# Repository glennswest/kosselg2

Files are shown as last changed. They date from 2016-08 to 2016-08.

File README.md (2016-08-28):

wolfstock
=========

__NOTE__ This is a Work In Progress

__NOTE__ The old T frame/Ostoc version of this has been deprecated and can be found in the branch [tframe](https://github.com/wolfmanjm/wolfstock/tree/tframe)

A 3d Delta printer based on the Mini-Kossel but using 2040 Makerslide for the
towers and the carriages, and accomodating larger bed and height.

* [Githubiverse page](http://wolfmanjm.github.com/wolfstock)
* [First Print](http://www.youtube.com/watch?v=khotvR7Lyf4)
* [Printing Tornado vase](http://www.youtube.com/watch?v=ChUlHnQ6QRw)
* [Printing](http://youtu.be/xLpwUxT9Mxs)
* [Swirling Urn print](http://flic.kr/p/fC9EcJ)

This is a Makerslide and Misumi based frame, using Spectra fishing
line drive ala original Kossel, or gt2 belts with crown pulleys.

It has a large frame made from 2040 and 2020 Misumi extrusion using
mini-kossel style printed brackets.

The default version has 1000mm high Makerslide towers, an 463.4mm triangle
sides, and arm length of 370mm, which makes for a roughly 250mm circular build
area using Traxxas joints and 400mm build height. Use the Kossel Calculator
and the lite-frame.scad to play with the exact lengths required. If you were
to use mag arms which have more degrees of movement the build area would be
around 350mm diameter for the above dimensions.

The drive system can use Spectra 60lb braided fishing line and machined spools
and 608 bearings for the idlers.

There is an alternate set of stls that make use of gt2 belt. In this case the
preferred idler is composed of two back to back 695 flanged bearings and the
`tensioner-gt2-F695zz.stl` file, but there is also a `crownedpulley.stl` that fits
over a 608 bearing and the file `tensioner_g2_608.stl` will house that. I have
found that the crowned pulleys do not seem to keep the belt aligned as they
are supposed to.

Most scad source files are parameterized so the dimensions can be
tweaked.

Some of the scad files are derived from Kossel files or other scad files, most
are original designs. The original source of the file is usually cited in the
code.

This work is licensed under the Creative Commons
Attribution-ShareAlike 3.0 Unported License. To view a copy of this
license, [visit](http://creativecommons.org/licenses/by-sa/3.0/)

## BoM

### Printed parts
Stls are in the
[STL directory](https://github.com/wolfmanjm/wolfstock/tree/master/stl)

* Print three `base-bracket-motor.stl`
* Print three `base-bracket-idler.stl`
* Print three `tensioner_608.stl` *OR* `tensioner_g2_608.stl` (also the `crownedpulley.stl` if using the latter) *OR* three `tensioner-gt2-F695zz.stl`
* Print one `effector.stl`
* Print three `carriage-new.stl` *OR* `gt2-carriage.stl` These bolt onto a carriage that has
  20mm hole paterns
  [like this](https://www.inventables.com/technologies/standard-wheel-carriage-plate),
  so check your plates and adjust the scad as necessary.
* Effector mounted extruder from http://www.thingiverse.com/thing:42112 with pg35l Stepper from http://www.ultibots.com/ (I use some aluminum stadoffs to raise the extruder about an inch.

### Extrusion and Vitamins
* 3x 1m lengths of 2040 Makerslide, OR 3x 1m lengths of Misumi 2040 and
  3x 1m lengths of open rail, OR 3x 1m lengths of 2040 V-Slot
* 3x 463.4mm lengths of 2040 for bottom rails (use the kossel
  calculator to get the length you want and add in the side offset,
  see the lite-frame.scad and play with the sizes)
* 3x 463.4mm lengths of 2020 for top rails
* 12x delrin v wheels for whatever rails you have chosen (sourcing
  below)
* Appropriate carriage for the rails and wheels, add 2x eccentric
  spacers per carriage and 3x regular spacers. (some wheels come with
  the regular ones)
* 6x 370mm 0.318" (8mm) square carbon fiber tube if using the endcaps to join
  with traxas joints, or round tubing as per Kossel like these from
  [Goodwinds](http://goodwinds.com/20015.html), where the traxxas joints may slip in with some hot glue
* plenty of t nuts and M5 bolts...
  lengths M5x16 for the back 18 total, M5x12 for the sides 32 total

## Sourcing

### Common components

* Bottom side rails [Misumi][] HFS5-2040-500 $5.40 3 $16.20
* Top side rails  [Misumi][] HFS5-2020-500 $2.85 3 $8.55
* Bolts for back of towers M5 Length 16mm
* Bolts for side braces M5 Length 12mm
* T Nuts M4 100 pack  [Misumi][] HNKK5-5 $20

### Drive Mechanism

Choose one of the following...

#### Fishing Line
* Spectra 60lb braided fishing line
* [Drive spools](http://3d.grabercars.com/?product=filament-drive-reel-grooved-delrin-18mm-o-d-for-kossel) $7.95 3 $23.85
* 3x 608 bearings for idler, and use tensioner_608.stl

#### GT2 Belt
* [GT2 Belt](http://www.robotdigg.com/product/10/Open-Ended-6mm-Width-GT2-Belt) $2.00/meter approx 6.3-7 meters $14.00
* [GT2 toothed pulley 20 Teeth 5mm Bore](http://www.robotdigg.com/product/9/GT2-Pulley-20-Teeth-5mm-Bore) $2.00 3 $6.00
* 3x 608 bearings and use `tensioner_g2_608.stl` idler and `crownedpulley.stl` OR
  6x F695zz flanged bearings and use `tensioner-gt2-F695zz.stl`, the latter seems to work better, and are
  [available here](http://www.ebay.com/itm/180915657724) 10 for $9.67 free shipping
* [Grub screws for pulley](http://www.robotdigg.com/product/17/M3*4-Grub-Screw-PACK-SET-for-Timing-Pulleys) $0.35

### Makerslide based
* [Makerslide rail 1000mm](https://www.inventables.com/technologies/makerslide) 25142-03 $21.74 3 $65.52
* [Dual Bearing V-Wheel Kit](https://www.inventables.com/technologies/dual-bearing-v-wheel-kit) 25203-02 $4.85 12 $58.20
* [Eccentric Spacer](https://www.inventables.com/technologies/eccentric-spacer) 25195-01 $2.00 6 $12.00
* [Nylon Spacer pack of 10](https://www.inventables.com/technologies/nylon-natural-color-spacer) 25206-01 $2.00 1 $2.00
* [Standard Wheel Carriage Plate](https://www.inventables.com/technologies/standard-wheel-carriage-plate) 25200-01 $8.00 3 $24.00

Sub Total: $161.72

### V Slot based
* [V-Slot 20 x 40mm 1000mm](http://openbuildspartstore.com/v-slot-20-x-40mm/) $13.00 3 $39.00
* [OpenBuilds Dual V Wheel Kit - Delrin](http://openbuildspartstore.com/openbuilds-dual-v-wheel-kit-delrin/) $3.85 12 $46.20
* [V-Slot Universal Plate](http://openbuildspartstore.com/v-slot-universal-plate) $12.00 3 $36.00
* [Eccentric Spacers](http://openbuildspartstore.com/eccentric-spacers/) $2.00 6 $12.00

Sub Total: $133.20

### Open Rail Based
* 2040 1000mm  [Misumi][] HFS5-2040-1000 $10.80 3 $32.40
* [Open Rail 1000mm](http://openbuildspartstore.com/openrail-black-anodized/) $6 6 $36
* [OpenBuilds Dual V Wheel Kit - Delrin](http://openbuildspartstore.com/openbuilds-dual-v-wheel-kit-delrin/) $3.85 12 $46.20
* [OpenRail Gantry Plate 40mm](http://openbuildspartstore.com/openrail-gantry-plate-universal-mount) $8.00 3 $24.00
* [Eccentric Spacers](http://openbuildspartstore.com/eccentric-spacers/) $2.00 6 $12.00

Sub Total: $150.60

### Printed carriage for Makerslide or Open Rail
For the cheapeast solution print `carriage-plate.stl` and just buy the v wheels.
This saves having to get the expensive aluminum plates and eccentric spacers.
That saves $36 on the open rail version and a lt more on the makerslide version.

* [OpenBuilds Dual V Wheel Kit - Delrin](http://openbuildspartstore.com/openbuilds-dual-v-wheel-kit-delrin/) $3.85 12 $46.20

### Notes
You can use the printed carriage for each tower, saving about $36 or more

## Assembly

1. Bolt the side rails in first to form the triangle. Remember to put
enough tslot nuts in the tslots first, also put some in the top and
side for mounting things later.
2. Mount the motors next.
3. Insert the Makerslide into the holes, use a rubber mallet to get the corners on the makerslide, but be gentle.
4. bolt the makerslide from the back.
5. do the same for the top, but remember to put the idlers in the track first

# License

<br /><span xmlns:dct="http://purl.org/dc/terms/" property="dct:title">Wolfstock</span> by <a xmlns:cc="http://creativecommons.org/ns#" href="http://wolfmanjm.github.com/wolfstock" property="cc:attributionName" rel="cc:attributionURL">Jim Morris</a> is licensed under a <a rel="license" href="http://creativecommons.org/licenses/by-sa/3.0/deed.en_US">Creative Commons Attribution-ShareAlike 3.0 Unported License</a>.<br />Based on a work at <a xmlns:dct="http://purl.org/dc/terms/" href="https://github.com/wolfmanjm/wolfstock" rel="dct:source">https://github.com/wolfmanjm/wolfstock</a>.

[Misumi]: http://www.misumi-ec.com "Misumi"

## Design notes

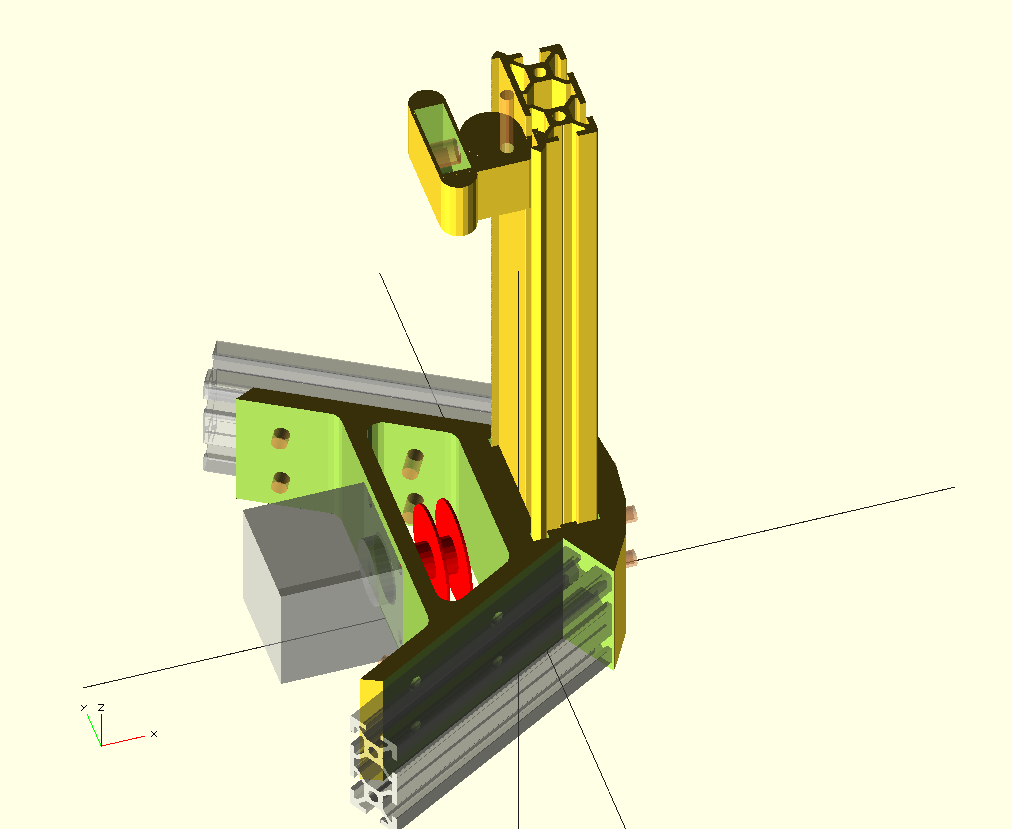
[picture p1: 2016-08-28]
img/belt-idler.png

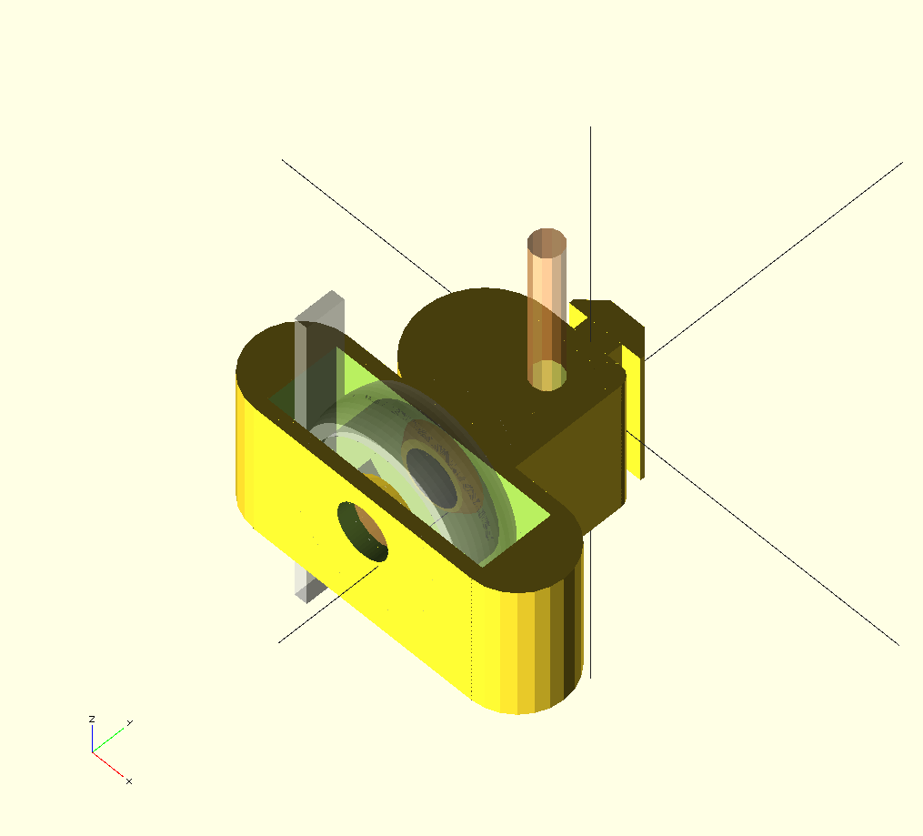
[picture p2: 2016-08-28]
img/g2-belt-idler.png

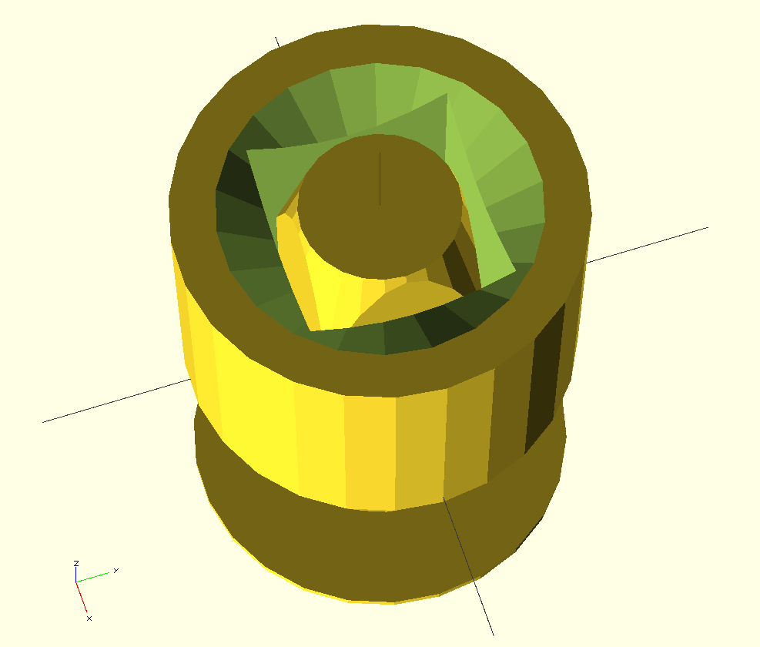
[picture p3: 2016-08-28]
img/rod-end.png

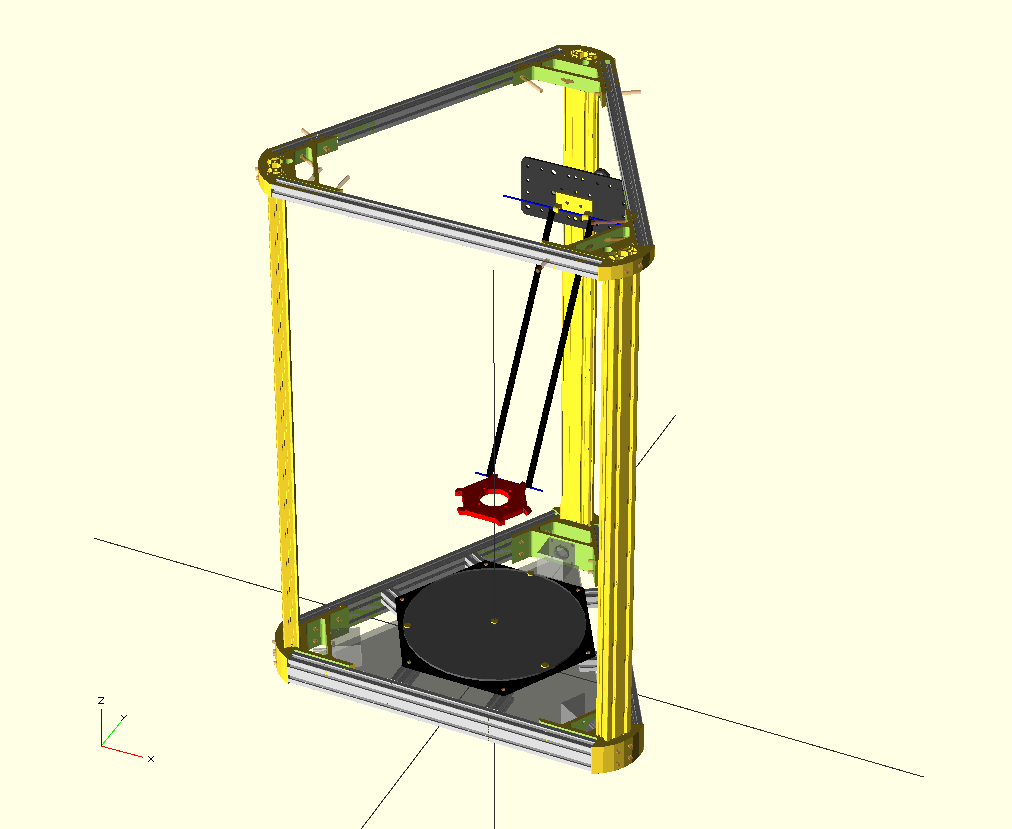
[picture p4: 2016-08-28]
img/lite-frame.png

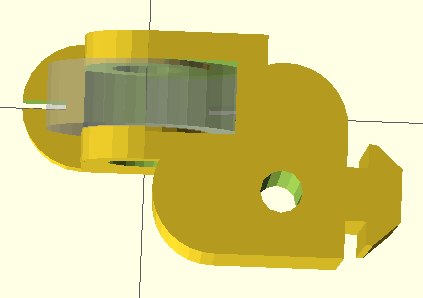
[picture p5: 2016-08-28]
img/tensioner-top.png

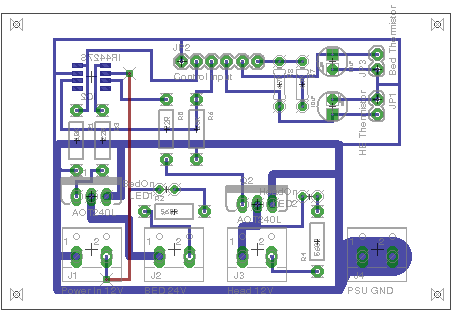
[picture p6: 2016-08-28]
circuits/mosfetpcb.png

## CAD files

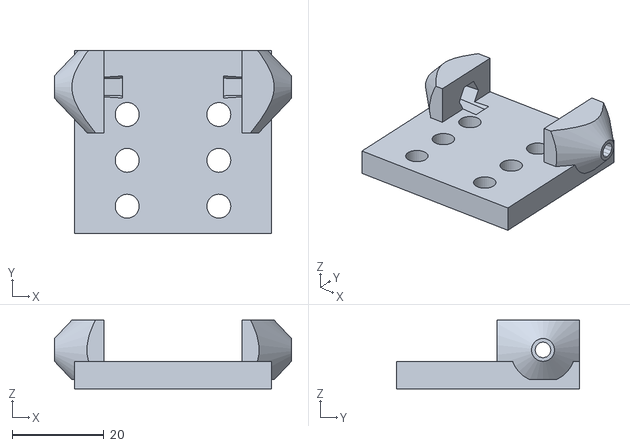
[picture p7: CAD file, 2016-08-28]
carriage-new.stl
51.7 x 40.0 x 15.0

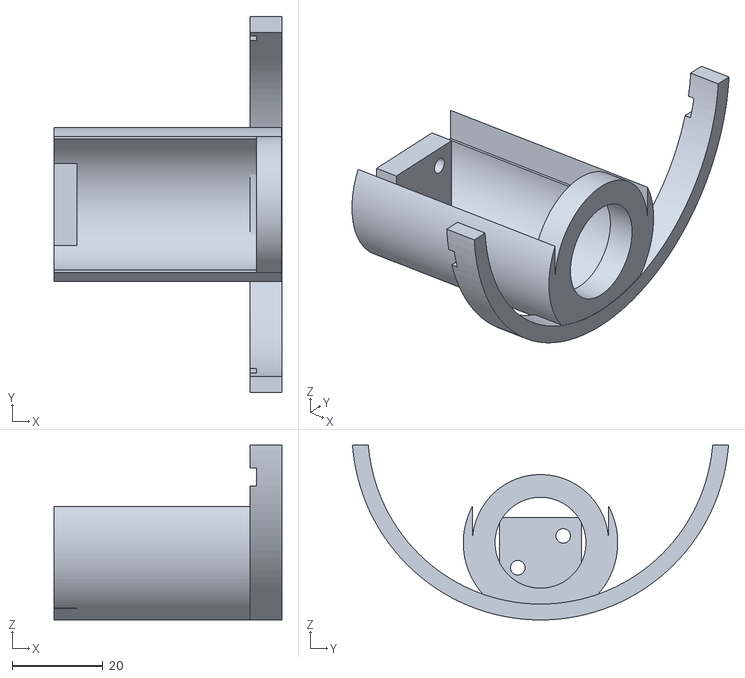
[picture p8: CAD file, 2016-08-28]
fixmount/sensormount.stl
50.1 x 82.8 x 38.5

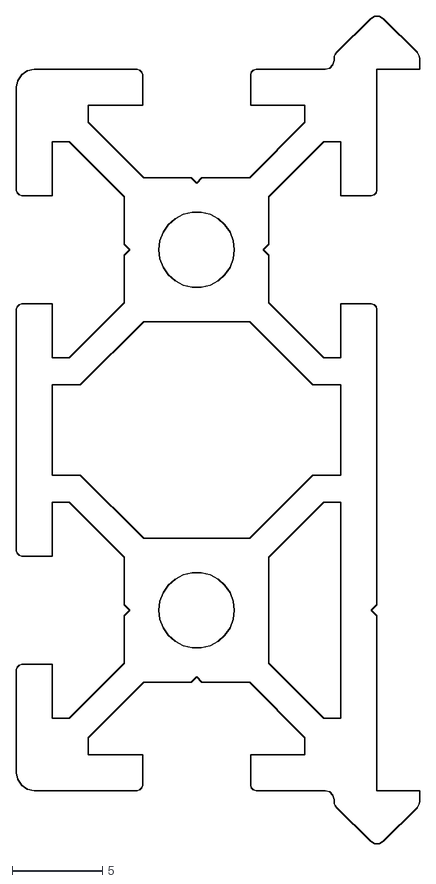
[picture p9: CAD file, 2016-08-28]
makerslide/makerslide_extrusion_profile.dxf
22.4 x 45.9

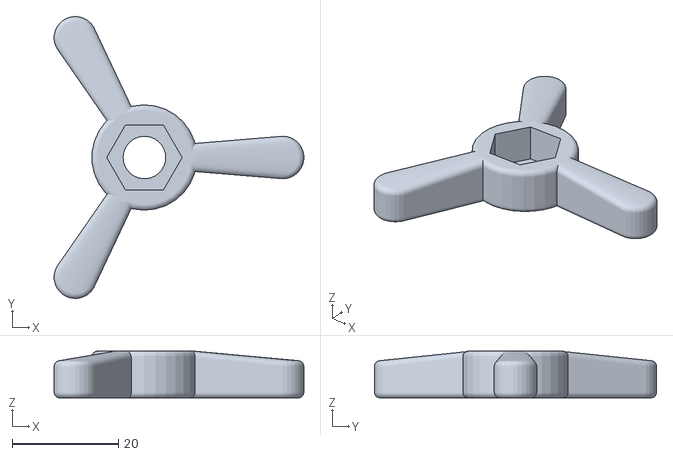
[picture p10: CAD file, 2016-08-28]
stl/thumbnut.stl
47.0 x 53.0 x 8.79

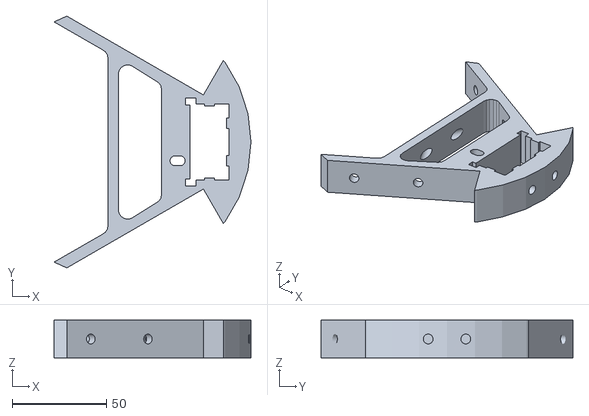
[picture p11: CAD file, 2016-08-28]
base-bracket-idler.stl
104.7 x 133.8 x 20.0

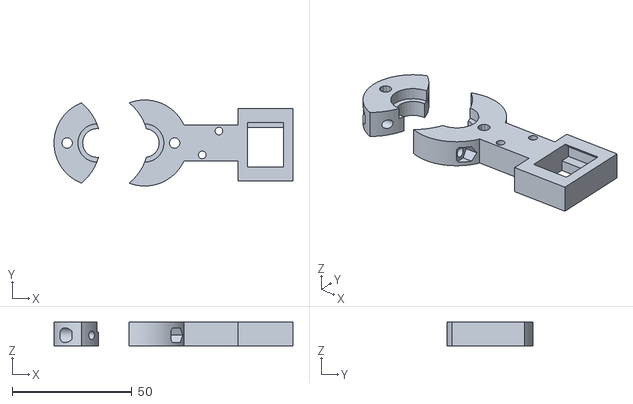
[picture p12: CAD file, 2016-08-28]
fixmount/e3dmountring.stl
100.0 x 36.0 x 10.0

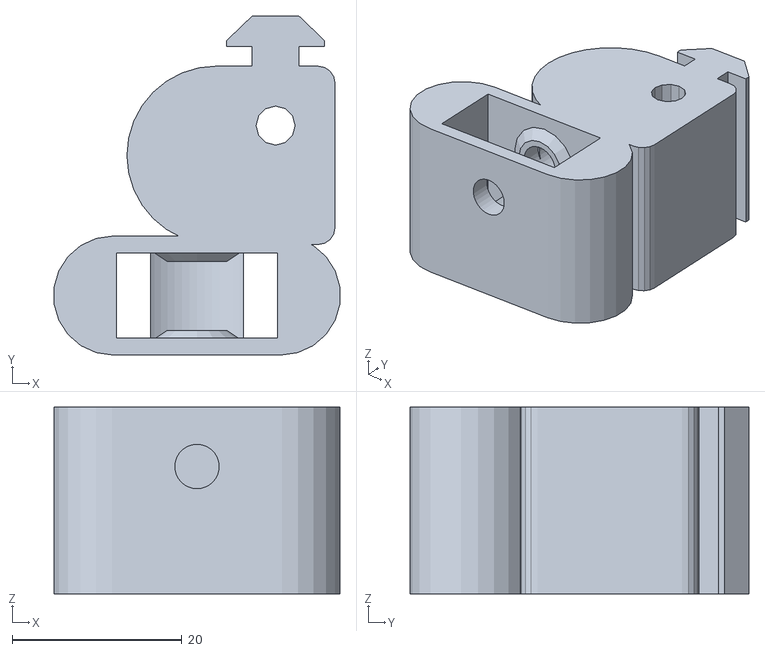
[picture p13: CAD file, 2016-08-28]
stl/tensioner-gt2-F695zz.stl
33.7 x 39.9 x 22.0

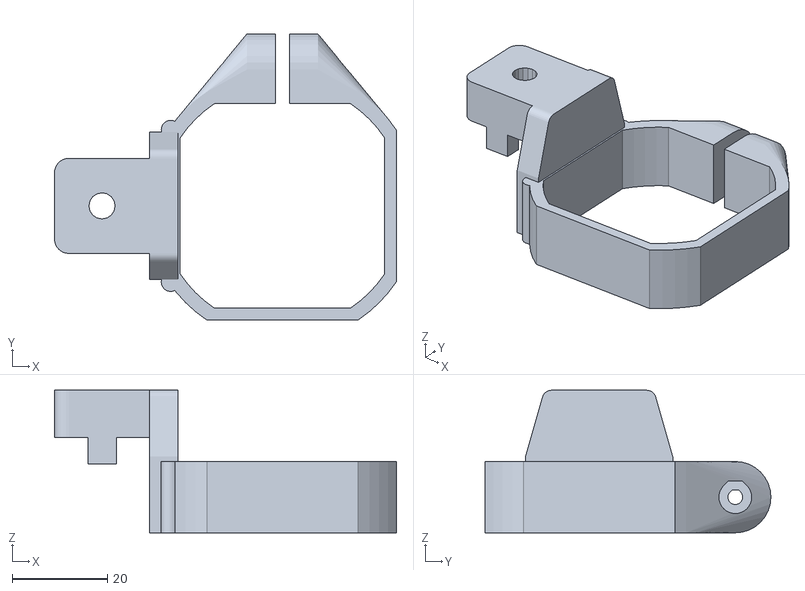
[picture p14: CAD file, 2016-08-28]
fixmount/nema17stepper-mount_v2.stl
72.0 x 60.1 x 30.0

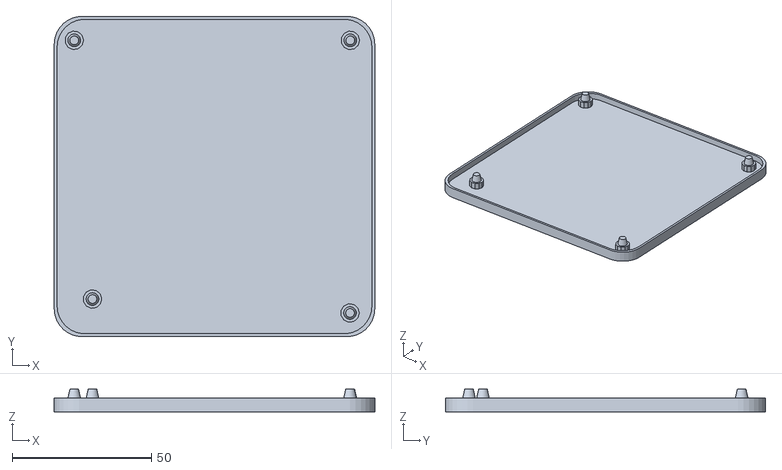
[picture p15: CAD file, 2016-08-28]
smoothie-box.stl
115.1 x 114.9 x 8.20

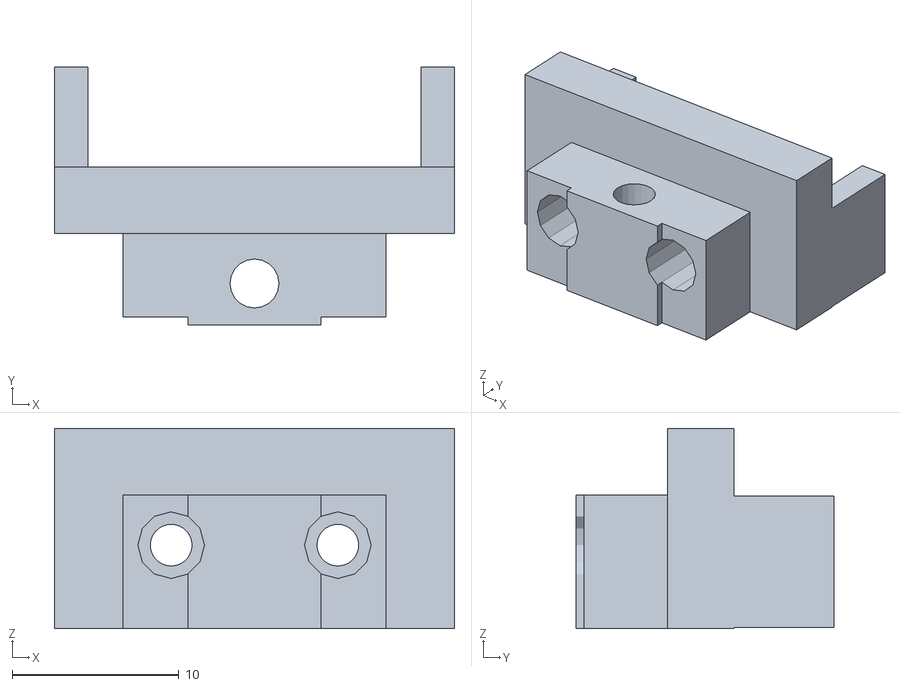
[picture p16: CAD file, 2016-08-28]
stl/adjustable-limit-stop-slide.stl
24.0 x 15.5 x 12.0

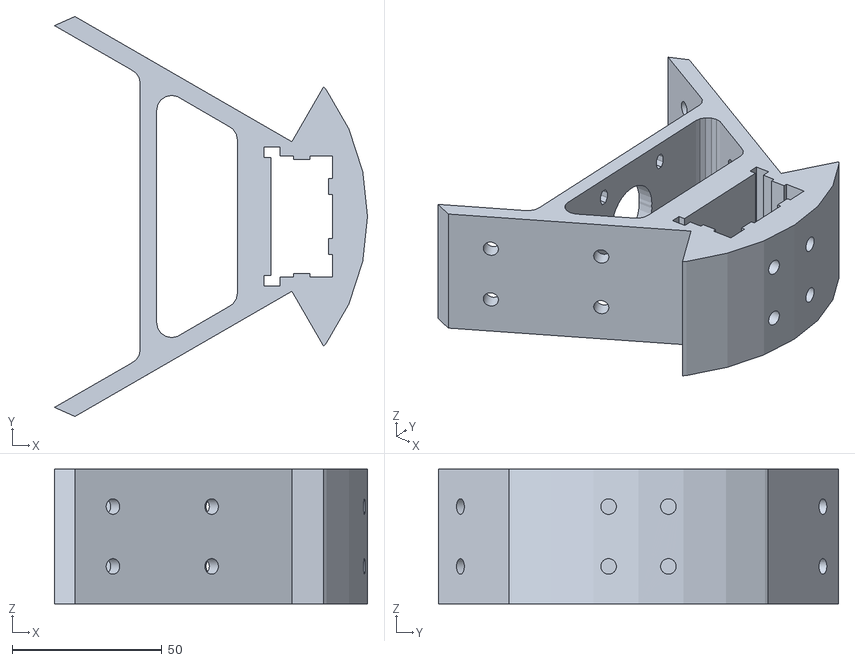
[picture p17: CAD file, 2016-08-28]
base-bracket-motor.stl
104.7 x 133.8 x 45.0

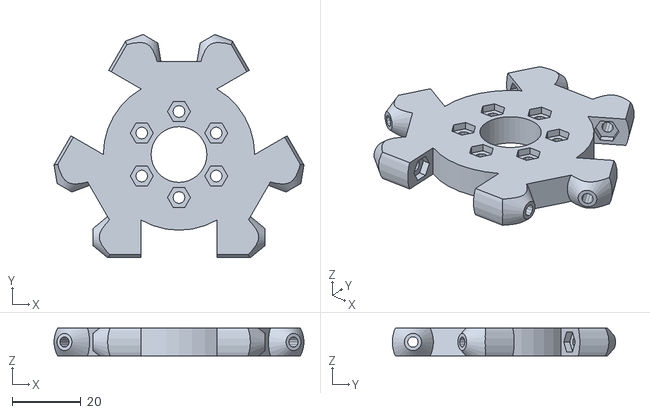
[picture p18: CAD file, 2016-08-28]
fixmount/effector50.stl
72.7 x 64.8 x 8.00

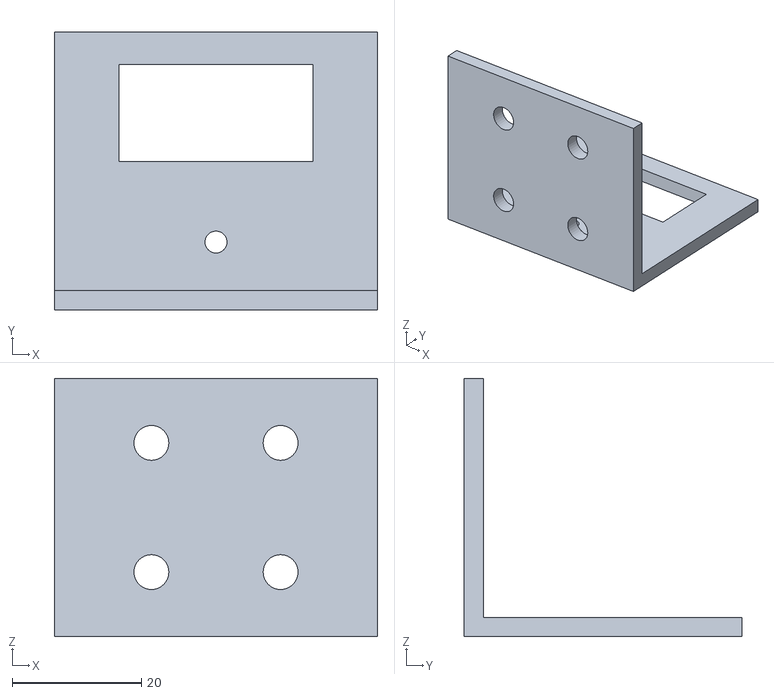
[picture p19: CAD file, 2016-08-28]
stl/eswitch-holder.stl
50.0 x 43.0 x 40.0

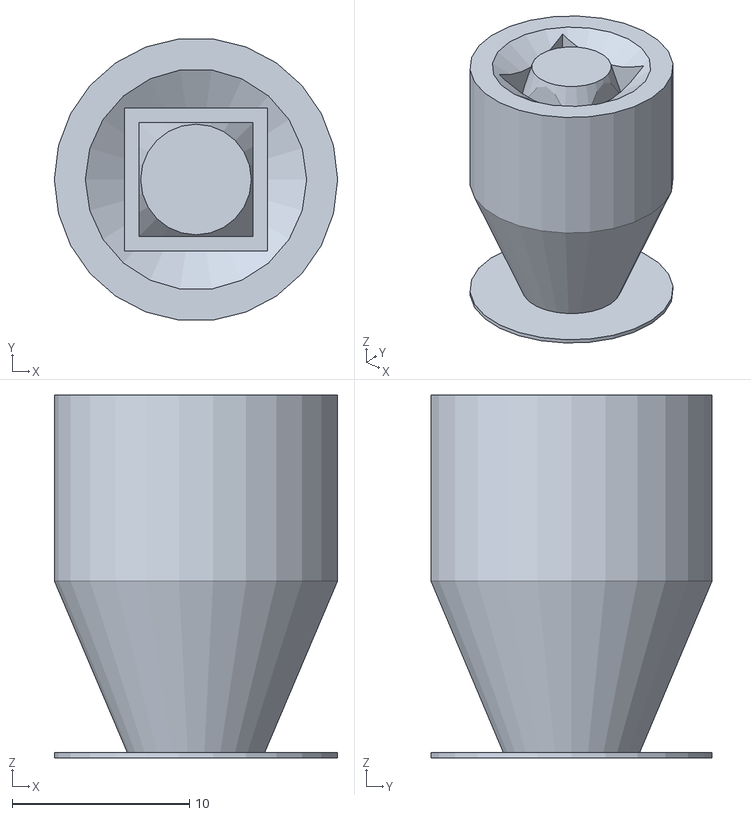
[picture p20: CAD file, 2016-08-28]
stl/rod-end-connector.stl
16.0 x 15.9 x 20.5

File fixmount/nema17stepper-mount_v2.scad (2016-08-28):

//remix of http://www.thingiverse.com/thing:528934
//
//-- NEMA 17 stepper holder for 2020 rail
//  designed by L Buell  Feb 2016
//-- remixed from a well designed remix by AndrewBCN - November 2014
//-- remixed from an original (excellent) design by Paul Chase
//-- original design is Thingiverse no. 321523

//  I removed some of AndrewBCN's stuff and added the 2020 mount
// some of my 2020 rail mounted designs are meant to be drop onto the rail,
//   and some are meant to more fully engage and slide in from the end of the rail
// this design is drop-in style

//-- slop is tolerance, wall is wall thickness
slop = 0.2; // don't mess with these two!
wall = 3;

base_plate_height = 16;
Vert_plate_thickness = 6; // vertical base plate thickness
motor_w = 42;
motor_r = 50/2;
$fn=32;
height = wall+12;
m5 = 5.5;           // threaded z-rod diameter
m3 = 3.3/2;     // diam of m3 screw
m3n = 6.9/2;  // diam of m3 nut
m3nh = 4;      // nut height of m3 nuts that hold adaptor to x-ends
m3nl = 20;     // screw length of nuts that hold adaptor to x-ends
hole_sep = 20;  // separation of mount holes - mount holes deleted - this now controls height of mount

rail_Ht=20;  //height of 2020 rail 
2020_mount_width=20;  // width of mounting arm on top of 2020 rail
2020_mount_thickness=10;  // thickness of mounting arm on top of 2020 rail
mount_radius=3;  //radius of corners of rounded block
2020_groove_size=6; //used for the width and depth of the block fitting into the 2020 rail
Tslot_nut_length=12;  //length of T-slot nut

complete_part();
//mirror(0,0,1) complete_part();

module complete_part(){
difference(){
union(){
stepper_holder();	
translate([-motor_w/2-2020_mount_width/2-Vert_plate_thickness-.95,0,10+hole_sep-2020_mount_thickness/2])2020_block();  //block that mounts into the 2020 rail
}  //union
// cavities

// 2020 mounting block cavities
translate([-motor_w/2-2020_mount_width/2-Vert_plate_thickness-.95,-2020_mount_width/2,0]){
//cutout for t-slot nut
translate([-2020_mount_width/2+rail_Ht/2-2020_groove_size/2-.5,(2020_mount_width-Tslot_nut_length)/2,rail_Ht-2020_groove_size-.5])cube([2020_groove_size+1,Tslot_nut_length,2020_groove_size+.5]);
// hole for t-slot nut
translate([-2020_mount_width/2+rail_Ht/2,2020_mount_width/2,rail_Ht+2020_mount_thickness/2])cylinder(h=rail_Ht, r=5.5/2,center=true,$fn=16);
}  // translate
}  //difference
}  //module

module 2020_block(){
rounded_rectangle([rail_Ht,2020_mount_width,2020_mount_thickness],mount_radius,center=true);
// fill in rounded corner
translate([rail_Ht/2-3,-2020_mount_width/2,-2020_mount_thickness/2])cube([Vert_plate_thickness,2020_mount_width,2020_mount_thickness]);
// square block to fit in slot on rail
translate([-2020_groove_size/2,-2020_mount_width/2,-2020_mount_thickness/2-2020_groove_size+.5])cube([2020_groove_size,2020_mount_width,2020_groove_size]);
}  //module 2020_block

module stepper_holder() {
	scale_slop = 1.025; // another tolerance
	scale_size = (motor_w+wall+wall)/motor_w;	
	difference(){
		union(){
			hull(){
				//strap
				scale([scale_size,scale_size,1]) motor_base(h=height);
				//clamp
				translate([0,motor_w/2+wall+m3+wall,height/2]) rotate([0,90,0]) cylinder(r=height/2, h=5*wall, center=true);			
			}
			//mount base
			hull(){
				// bottom block of mount
				translate([-motor_w/2-wall-wall/2+0.55,0,base_plate_height/2]) cube([Vert_plate_thickness,31,base_plate_height], center=true);
				//  top cylinders that make top of mount
				translate([-motor_w/2-wall-wall/2+0.55-Vert_plate_thickness/2,+10,8+hole_sep]) rotate([0,90,0]) cylinder(r=2, h=Vert_plate_thickness);
				translate([-motor_w/2-wall-wall/2+0.55-Vert_plate_thickness/2,-10,8+hole_sep]) rotate([0,90,0]) cylinder(r=2, h=Vert_plate_thickness);				
			}
			// reinforcement cylinders in corners
			translate([-motor_w/2-wall-wall+3.5,+16,0]) rotate([0,0,0]) cylinder(r=2, h=15);
			translate([-motor_w/2-wall-wall+3.5,-16,0]) rotate([0,0,0]) cylinder(r=2, h=15);
		}  //union

		//cavities
		// slit
		translate([0,motor_w/2,height/2]) cube([wall,motor_w,height+1],center=true);
		// clamp holes
		render() translate([0,motor_w/2+wall+m3+wall,height/2]) rotate([0,90,0]) clamp_holes();
		// motor cross section hollowed out
		scale([scale_slop,scale_slop,1]) translate([0,0,-.05]) motor_base(h=height+.1);
	}
	
	// uncomment this if you need a place to tie wires to
	/*
	//-- AndrewBCN: I added a place where people can tie some wires
	difference(){
	   rotate([0,0,-90]) translate([22.5,+8,0]) cube([8,8,4]);
	   rotate([0,0,-90]) translate([26.5,+10,-2]) cube([1.5,4,12]);
	}
	*/	
} //module stepper_holder

module clamp_holes() {
	len = wall*5;
	// screwhole
	rotate([0,0,-90]) cap_cylinder(r=3.1/2, h=len*2, center=true); 
	// nut is on the inside
	mirror([0,0,1]) translate([0,0,wall*2.5]) rotate([0,0,-90]) cylinder(r=6.9/2, h=len, $fn=6);
	// screw is on the outside
	translate([0,0,wall*2.5]) rotate([0,0,-90]) cap_cylinder(r=6.9/2, h=len);
}

module cap_cylinder(r=1, h=1, center=false){
	render() union() {
		cylinder(r=r, h=h, center=center);
		intersection(){
			rotate([0,0,22.5]) cylinder(r=r/cos(180/8), h=h, $fn=8, center=center);
			translate([0,-r/cos(180/4),0]) rotate([0,0,0]) cylinder(r=r/cos(180/4), h=h, $fn=4, center=center);
		}
	}
}

//-- Motor cross section
module motor_base(h=wall){
	intersection(){
		translate([0,0,h/2]) cube([motor_w, motor_w, h], center=true);
		cylinder(r=motor_r+slop, h=h, $fn=64);
	}
}

// From: https://github.com/T3P3/Mendel90/tree/LaserCut/scad
// utils.scad
module rounded_square(w, h, r){
    union() {
        square([w - 2 * r, h], center = true);
        square([w, h - 2 * r], center = true);
        for(x = [-w/2 + r, w/2 - r])
            for(y = [-h/2 + r, h/2 - r])
                translate([x, y])
                    circle(r = r);
    }
}
// From: https://github.com/T3P3/Mendel90/tree/LaserCut/scad
// utils.scad
module rounded_rectangle(size, r, center = true){
    w = size[0];
    h = size[1];
    linear_extrude(height = size[2], center = center)
        rounded_square(size[0], size[1], r);
}

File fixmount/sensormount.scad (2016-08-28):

// main module
rotate([0,90,0])main();

$fn=128;

module main() {
  
  difference(){
      translate([ -4,-9,-4.5]) cube([20,18,5]);
      translate([  7,-5,-5.5]) cylinder(r=1.6,h=12);
      translate([  0,+5,-5.5]) cylinder(r=1.6,h=12);
      }
   
   difference(){
       union(){
         translate([11,-7.5,-4.5]) cube([5,15,50]);  
         translate([1.5,0,-4.5]) cylinder(r=17,h=50);
       }
       translate([1.5,0,-5.5]) cylinder(r=14.5,h=53);
       translate([-30,-15,-5.5]) cube([30,30,52]);
       }
      difference(){ 
        translate([1.5,0, 40]) cylinder(r=15,h=5.5);  //9.5
        translate([1.5,0, 39.2]) cylinder(r=10,h=6.4);
        }
      difference(){  
        translate([-23.0,0,38.6]) cylinder(r=41.5,h=7);
        translate([-23.0,0,36.6]) cylinder(r=38,h=10);
        translate([ -104,-42,38]) cube([84,84,12]);
        translate([ -15,-42,28]) cube([4,84,12]);  
        }  
      
  }

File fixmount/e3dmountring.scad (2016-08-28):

// J-Head (E3D) mount
// copyright (c) 2013 - Jarek Szczepanski <imrahil@imrahil.com>
// oryginal design derived from http://www.thingiverse.com/thing:26355

use <keystone.scad>

$fn=256;

size = 18;
length = 28;
height = 9;

separation = 50;  // Distance between ball joint mounting faces.
offset = 20;  // Same as DELTA_EFFECTOR_OFFSET in Marlin.
mount_radius = 12.5;  // Hotend mounting screws, standard would be 25mm.
hotend_radius = 8.1;  // Hole for the hotend (J-Head diameter is 16mm).
push_fit_height = 4;  // Length of brass threaded into printed plastic.
height = 10;
cone_r1 = 2.5;
cone_r2 = 14;


mount_spacing = 50;
carriage_mount_dia = 4.5;

// dimensions for E3D hotned
extruder_dia = 16;
extruder_dia2 = 12;
extruder_cyl1_height = 3.7;
extruder_cyl2_height = 5.6;

mount_screws_dia = 3.5;

// Increase this if your slicer or printer make holes too tight.
extra_radius = 0.1;

// OD = outside diameter, corner to corner.
m3_nut_od = 6.1;
m3_nut_radius = m3_nut_od/2 + 0.2 + extra_radius;

// Major diameter of metric 3mm thread.
m3_major = 2.85;
m3_radius = m3_major/2 + extra_radius;
m3_wide_radius = m3_major/2 + extra_radius + 0.2;


// main module
main();

module main() {
  translate([62,-16,-4.5]) rotate([0,0,90]) keystone();
  difference(){
      translate([16,-7.5,-4.5]) cube([23,15,height]);
      translate([31,+5,-5.5]) cylinder(r=1.6,h=12);
      translate([24,-5,-5.5]) cylinder(r=1.6,h=12);
      }
  translate([-20, 0, 0]){
    intersection() {
      mount();
      separator();
    }
  }

  difference() {
    mount();
    separator();
  }
}

module mount() {
  difference() {
    plate();
    extruder();
    mount_screws();
  }
}

module plate() {
  difference() {
  
       translate([0,0,-4.5]) cylinder(r=18, h=height);
   
   
  for (a = [90:180:359]) rotate([0, 0, a]) {
      translate([0, mount_radius, 0])
	cylinder(r=m3_wide_radius+.5, h=2*height, center=true, $fn=12); // Add /5 to give us room for brass
    //  translate([0, mount_radius, height-4.4]) 
    //    cylinder(r=m3_nut_radius, h=3, center=true, $fn=6);
    }  
  }
}

module extruder() {
  pos1 = height/2 - extruder_cyl1_height/2 + 0.5;
  pos2 = height/2 - extruder_cyl1_height - extruder_cyl2_height/2;

  union() {
    translate([0, 0, pos1]){
      cylinder(r=extruder_dia/2, h=extruder_cyl1_height + 1, center=true, $fn=32); 
    }

    translate([0, 0, pos2]){
       cylinder(r=extruder_dia2/2, h=extruder_cyl2_height + 1, center=true, $fn=32); 
    }	
  }
}

module mount_screws() {
  union() {
    translate([0, 12, 0]){
      rotate([0, 90, 0]) cylinder(r=mount_screws_dia/2, h=length + 3, center=true, $fn=32); // hole for nut
      translate([length/2 - 3, 0, 0]){
        rotate([-90, 0, -90]) cylinder(r=mount_screws_dia, h=5, $fn=6); 
      }
      translate([-length/2 - 1.5, 0, 0]){
        rotate([0, 90, 0]) cylinder(r=3.1, h=5, $fn=32); // hole for screw's head
      }
    }

    translate([0, -12, 0]){
      rotate([0, 90, 0]) cylinder(r=mount_screws_dia/2, h=length + 3, center=true, $fn=32); // hole for nut 
      translate([length/2 - 3, 0, 0]){
        rotate([-90, 0, -90]) cylinder(r=mount_screws_dia, h=5, $fn=6); 
      }
      translate([-length/2 - 1.5, 0, 0]){
        rotate([0, 90, 0]) cylinder(r=3.1, h=5, $fn=32); // hole for screw's head 
      }
    }
  }
}

module separator() {
  translate([-20, 0, 0]){
    cylinder(r=43/2, h=height + 1, center=true, $fn=64); 
  }
}

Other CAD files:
stl/adjustable-limit-stop.stl
stl/adjustable-limit-stop-mount.stl
stl/carriage-plate.stl
stl/2020-insert.stl
configuration.scad
2020-insert.scad
MCAD/bearing.scad
MCAD/bitmap/alphabet_block.scad
MCAD/bitmap/bitmap.scad
MCAD/bitmap/height_map.scad
MCAD/bitmap/letter_necklace.scad
MCAD/bitmap/name_tag.scad
MCAD/boxes.scad
MCAD/constants.scad
MCAD/curves.scad
MCAD/gears.scad
MCAD/gridbeam.scad
MCAD/hardware.scad
MCAD/involute_gears.scad
MCAD/materials.scad
MCAD/math.scad
MCAD/metric_fastners.scad
MCAD/motors.scad
MCAD/nuts_and_bolts.scad
MCAD/regular_shapes.scad
MCAD/screw.scad
MCAD/servos.scad
MCAD/shapes.scad
MCAD/stepper.scad
MCAD/teardrop.scad
MCAD/triangles.scad
MCAD/units.scad
MCAD/utilities.scad
Orbitron_Medium.scad
arm-mount.scad
arm-plate.scad
base-bracket-idler.scad
base-bracket-motor.scad
card.scad
carriage-new.scad
carriage-plate.scad
carriage_plate_standard_c14005_rev_2.scad
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

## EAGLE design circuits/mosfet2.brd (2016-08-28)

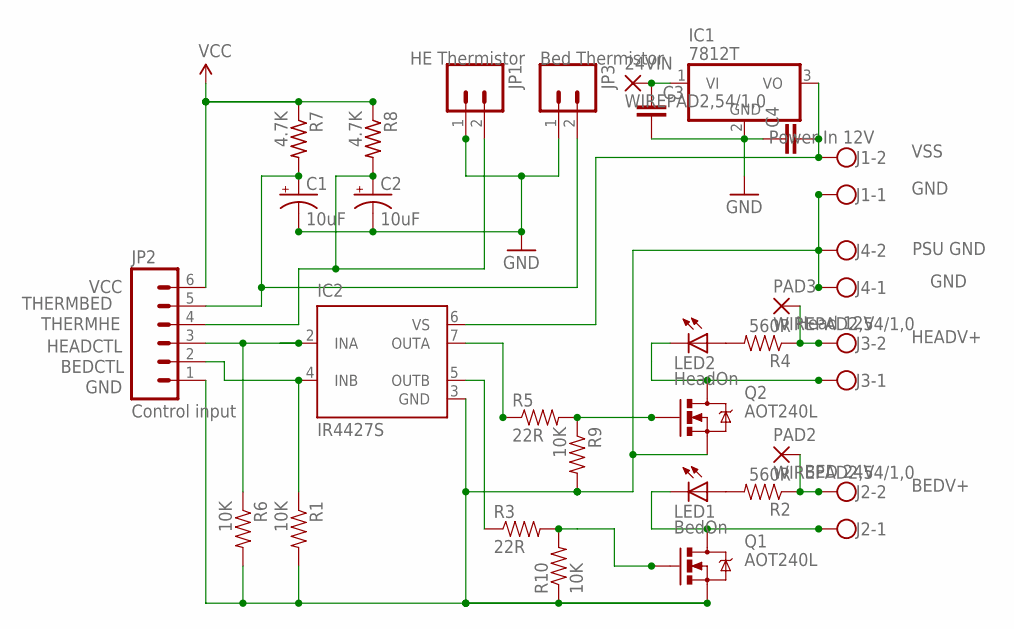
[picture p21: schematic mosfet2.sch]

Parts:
24VIN: WIREPAD2,54/1,0; 2,54/1,0
C1, C2: 10uF; CPOL-RADIAL-10UF-25V
C3, C4: CAPEZ; CAP-PTH-SMALLEZ
IC1: 7812T; TO220H
IC2: IR4427S; SO08
J1: Power In 12V; W237-102
J2: BED 24V; W237-102
J3: Head 12V; W237-102; MPN 237-102
J4: PSU GND; W237-102
JP1: HE Thermistor; 1X02
JP2: Control input; 1X06
JP3: Bed Thermistor; 1X02
LED1: BedOn; LED3MM-NS
LED2: HeadOn; LED3MM-NS
PAD2, PAD3: WIREPAD2,54/1,0; 2,54/1,0
Q1, Q2: AOT240L; TO220V
R1, R6, R9, R10: 10K; AXIAL-0.4
R2, R4: 560R; AXIAL-0.4
R3, R5: 22R; AXIAL-0.4
R7, R8: 4.7K; 0204/7

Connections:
BEDCTL: IC2.4 (INB), JP2.2, R1.P$1 (1)
BEDV+: J2.2, PAD2.1, R2.P$1 (1)
GND: C1.2 (-), C2.2 (-), C3.2, C4.1, IC1.2 (GND), IC2.3 (GND), J1.1, J4.1, J4.2, JP1.1, JP2.1, JP3.1, Q1.3 (S), Q2.3 (S), R1.P$2 (2), R6.P$2 (2), R9.P$2 (2), R10.P$1 (1)
HEADCTL: IC2.2 (INA), JP2.3, R6.P$1 (1)
HEADV+: J3.2, PAD3.1, R4.P$1 (1)
unnamed: 24VIN.1, C3.1, IC1.1 (VI)
unnamed: IC2.5 (OUTB), R3.P$1 (1)
unnamed: Q1.1 (G), R3.P$2 (2), R10.P$2 (2)
unnamed: LED1.A, R2.P$2 (2)
unnamed: J2.1, LED1.K (C), Q1.2 (D)
unnamed: LED2.A, R4.P$2 (2)
unnamed: Q2.1 (G), R5.P$2 (2), R9.P$1 (1)
unnamed: IC2.7 (OUTA), R5.P$1 (1)
unnamed: J3.1, LED2.K (C), Q2.2 (D)
THERMBED: C1.1 (+), JP2.5, JP3.2, R7.2
THERMHE: C2.1 (+), JP1.2, JP2.4, R8.2
VCC: JP2.6, R7.1, R8.1
VSS: C4.2, IC1.3 (VO), IC2.6 (VS), J1.2

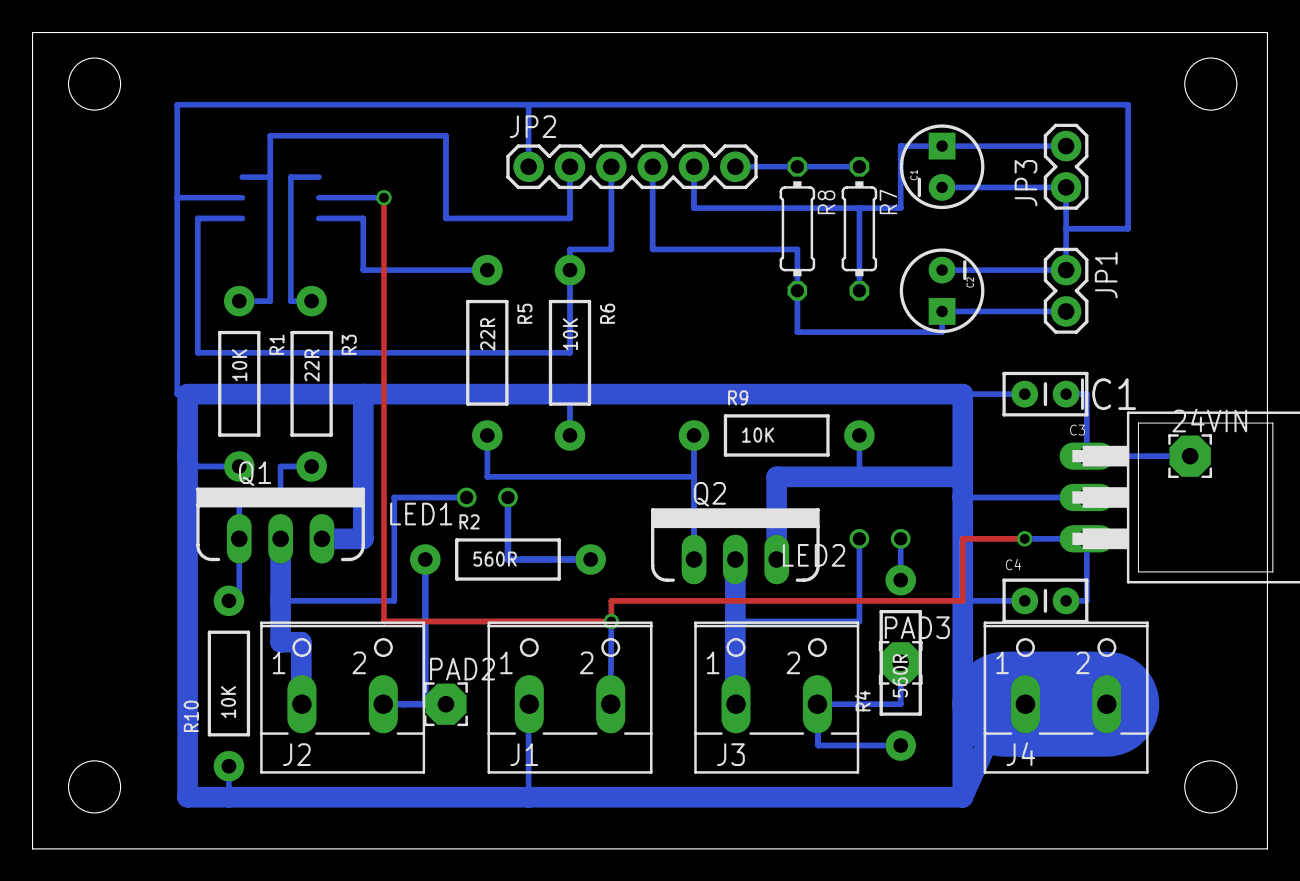
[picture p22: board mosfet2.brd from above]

Board: 2 copper layers, 75.9 x 50.2 mm, 30 parts (1 on the bottom side), 18 nets.

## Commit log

2016-08-28 Push updates
    [2020-insert.scad, 2020-insert.stl, Orbitron_Medium.scad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]
2016-08-28 Render it for brass fit
    [e3dmountring.stl]
2016-08-28 Treak screw holes and add cable ties for led ring
    [sensormount.scad, sensormount.stl]

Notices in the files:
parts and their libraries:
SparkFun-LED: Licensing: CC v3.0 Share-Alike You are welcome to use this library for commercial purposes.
